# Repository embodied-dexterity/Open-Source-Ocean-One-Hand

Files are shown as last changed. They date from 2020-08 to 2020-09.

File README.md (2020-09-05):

# Open-Source-Ocean-One-Hand
Welcome to the Open Source Ocean One Hand Project. Here are the files you need to create your own Ocean One hand. Each folder is one subassembly, and it 
contains CAD files for each individul parts and the subassembly which are readable by SolidWorks. The folders also contain files for parts that are 
for prototyping, such as 3D printing, laser cutting and rubber casting. \
The instruction manual attached provides not only the assembly instruction, but also the off-the-shelf parts shopping list and some other key protytping notes. \
Please do not hesistate to give us feedbacks or questions regarding this project as we need your help to make this project more accessible to people who would like to learn more about robotics. 
We look forward to all your comments!! \
Thank you for your interest in the Open Source Ocean One Hand Project.

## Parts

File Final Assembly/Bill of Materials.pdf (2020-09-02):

ITEM NO. | PART NUMBER | DESCRIPTION | QTY.
1 | 92290A182 | Shoulder Bolt | 4
2 | Finger Mounting Plate Assembly | | 1
3 | eyehook plate with side slots | | 1
4 | 94150A335 | Hex Nut | 4
5 | Rubber Palm Plate | | 1
6 | 90116A153 | Pan Head Phillips Machine Screw | 7
7 | shaft support | | 1

SOLIDWORKS Educational Product. For Instructional Use Only.

This is a Top Level only part list. To see part lists of sub-assembly, please refer to the Bill of Materials in the folder of each sub-assembly

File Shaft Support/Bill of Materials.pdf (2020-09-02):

ITEM NO. | PART NUMBER | DESCRIPTION | QTY.
1 | Shaft Suppot | | 1
2 | Torsional Spring Hub | | 3
3 | 7532K11 | Thrust Washer | 4
4 | Custom D-Shaft | | 1
5 | 7763K1 | Bushing | 2
6 | 30425T23 | Eye Hook for Wood | 3

SOLIDWORKS Educational Product. For Instructional Use Only.

This is a Top Level only part list. To see part lists of sub-assembly, please refer to the Bill of Materials in the folder of each sub-assembly

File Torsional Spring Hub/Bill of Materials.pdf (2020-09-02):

ITEM NO. | PART NUMBER | DESCRIPTION | QTY.
1 | Torsional Spring Coupler | | 1
2 | SpringInsideSpacer | | 1
3 | 7532K11 | Thrust Washer | 1
4 | Torsional Spring Hub Pulley | | 1
5 | 9287K143 | Torsional Spring | 1
6 | 6679K11 | Bushing | 1
7 | 93935A310 | Thin Hex Nut | 1
8 | 92029A097 | Cup Point Set Screw | 1
9 | 93600A200 | Dowel Pin | 1

SOLIDWORKS Educational Product. For Instructional Use Only.

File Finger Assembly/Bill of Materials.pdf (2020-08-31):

ITEM NO. | PART NUMBER | DESCRIPTION | QTY.
1 | distal finger | | 1
2 | mid finger | | 1
3 | 93600A195 | Dowel Pin | 1
4 | 93600A376 | Dowel Pin | 1
5 | 93600A246 | Dowel Pin | 1
6 | 93600A163 | Dowel Pin | 2
7 | 93600A249 | Dowel Pin | 2
8 | 93600A233 | Dowel Pin | 2
9 | 93600A238 | Dowel Pin | 2
10 | 93600A223 | Dowel Pin | 1
11 | Distal Flexure | | 2
12 | Middle Flexure | | 2
13 | 92398A121 | Hex Shaped Insert | 4
14 | 90116A153 | Pan Head Philips Machine Screw | 4
15 | Proximal Joint | | 1
16 | Base Joint | | 1
17 | 6362K1 | Dry Running Sleeve Bearing | 2
18 | 90101A009 | Nylon Inser locknut | 1
19 | 94035A172 | Shoulder Screw | 1
20 | 9287K208 | Torsion Spring | 1

SOLIDWORKS Educational Product. For Instructional Use Only.

There are extra parts not listed here as they are not in the SolidWorks Assembly but they are listed in the instruction.

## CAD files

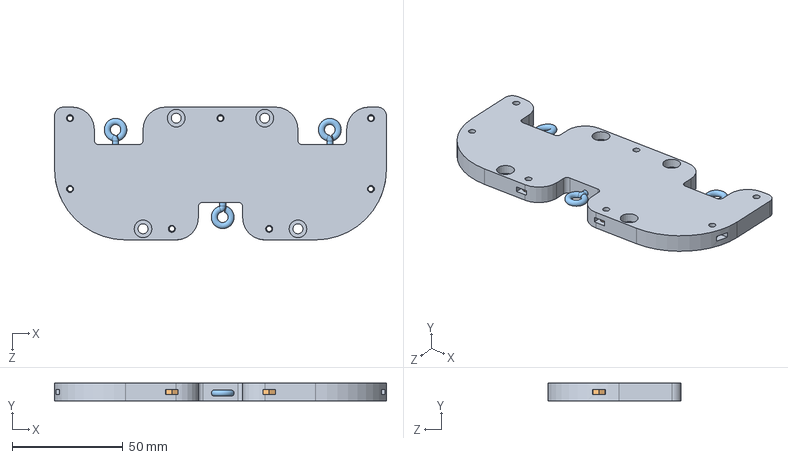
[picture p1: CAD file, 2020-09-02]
Eyehook Plate/eyehook plate with side slots.SLDASM
150.0 x 8.00 x 60.0 mm
eyeHookMountingPlate
94150A325_TYPE 316 STAINLESS STEEL HEX NUT x 7
eyeHook_forWood_30425T230 x 3

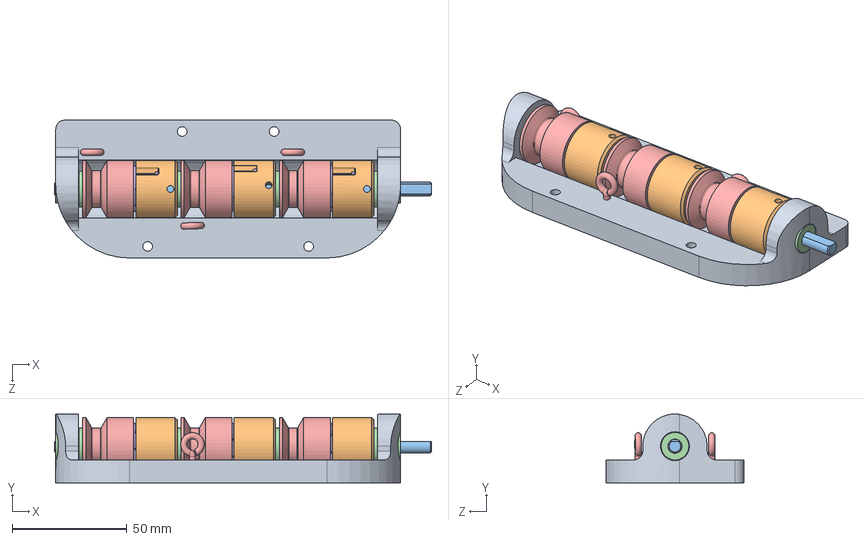
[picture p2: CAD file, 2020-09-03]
Final Assembly/shaft support.SLDASM
164.0 x 30.0 x 60.0 mm
Shaft Suppot
Torsional Spring Coupler x 3
SpringInsideSpacer x 3
6mmThrustWasher_7532K110 x 7
Torsional Spring Hub Pulley x 3
torsionalSpring_9287K143 x 3
m6Bushing_6679K110 x 3
93935A310_TYPE 316 SS THIN HEX NUT - DIN 439B x 3
92029A097_TYPE 316 STAINLESS STEEL CUP POINT SET SCREW x 3
93600A200_METRIC TYPE 316 STAINLESS STEEL DOWEL PIN x 3
Custom D-Shaft
m6Bushing_7763K100 x 2
eyeHook_forWood_30425T230 x 3

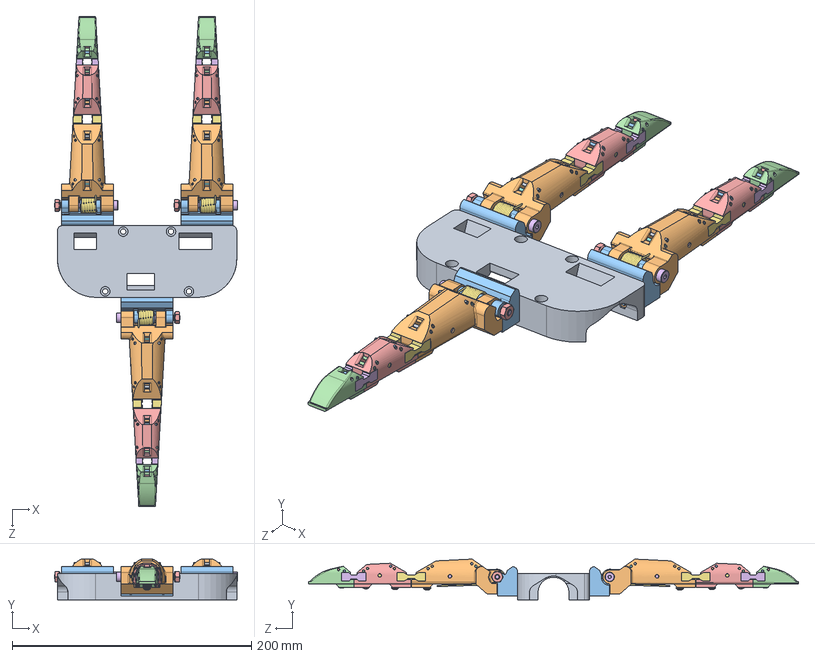
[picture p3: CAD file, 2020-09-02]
Final Assembly/Finger Mounting Plate Assembly.SLDASM
153.2 x 34.2 x 409.8 mm
Finger Mounting plate
94150A325_TYPE 316 STAINLESS STEEL HEX NUT x 6
M3x25_flathead_92010A130 x 6
distal finger x 3
mid finger x 3
93600A195_316 STAINLESS STEEL DOWEL PIN x 3
93600A376_METRIC TYPE 316 STAINLESS STEEL DOWEL PIN (1) x 3
93600A246_316 STAINLESS STEEL DOWEL PIN x 3
93600A163_316 STAINLESS STEEL DOWEL PIN x 6
93600A249_METRIC TYPE 316 STAINLESS STEEL DOWEL PIN x 6
93600A233_METRIC TYPE 316 STAINLESS STEEL DOWEL PIN x 6
93600A238_METRIC TYPE 316 STAINLESS STEEL DOWEL PIN x 6
93600A223_METRIC TYPE 316 STAINLESS STEEL DOWEL PIN x 3
Distal Flexure x 6
Middle Flexure x 6
92398A121_18-8 SS TWIST-RESISTANT HEX-SHAPED INSERTS (1) x 12
90116A153_METRIC 316 SS PAN HEAD PHILLIPS MACHINE SCREW x 12
Proximal Joint x 3
Base Joint x 3
6362K100_WATER-RESISTANT DRY-RUNNING SLEEVE BEARING (1) x 6
90101A009_TYPE 18-8 SS THIN NYLON-INSERT LOCKNUT x 3
94035A172_18-8 STAINLESS STEEL PRECISION SHOULDER SCREW (1) x 3
9287K208_302 STAINLESS STEEL TORSION SPRING x 3

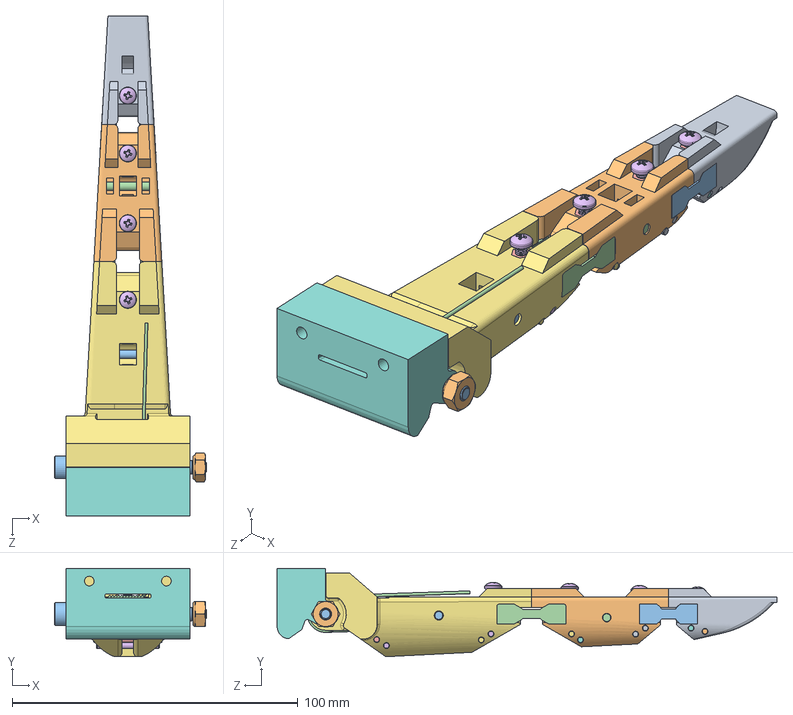
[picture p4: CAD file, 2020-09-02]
Finger Mounting Plate/Finger Assembly.SLDASM
53.2 x 30.9 x 174.9 mm
distal finger
mid finger
93600A195_316 STAINLESS STEEL DOWEL PIN
93600A376_METRIC TYPE 316 STAINLESS STEEL DOWEL PIN (1)
93600A246_316 STAINLESS STEEL DOWEL PIN
93600A163_316 STAINLESS STEEL DOWEL PIN x 2
93600A249_METRIC TYPE 316 STAINLESS STEEL DOWEL PIN x 2
93600A233_METRIC TYPE 316 STAINLESS STEEL DOWEL PIN x 2
93600A238_METRIC TYPE 316 STAINLESS STEEL DOWEL PIN x 2
93600A223_METRIC TYPE 316 STAINLESS STEEL DOWEL PIN
Distal Flexure x 2
Middle Flexure x 2
92398A121_18-8 SS TWIST-RESISTANT HEX-SHAPED INSERTS (1) x 4
90116A153_METRIC 316 SS PAN HEAD PHILLIPS MACHINE SCREW x 4
Proximal Joint
Base Joint
6362K100_WATER-RESISTANT DRY-RUNNING SLEEVE BEARING (1) x 2
90101A009_TYPE 18-8 SS THIN NYLON-INSERT LOCKNUT
94035A172_18-8 STAINLESS STEEL PRECISION SHOULDER SCREW (1)
9287K208_302 STAINLESS STEEL TORSION SPRING

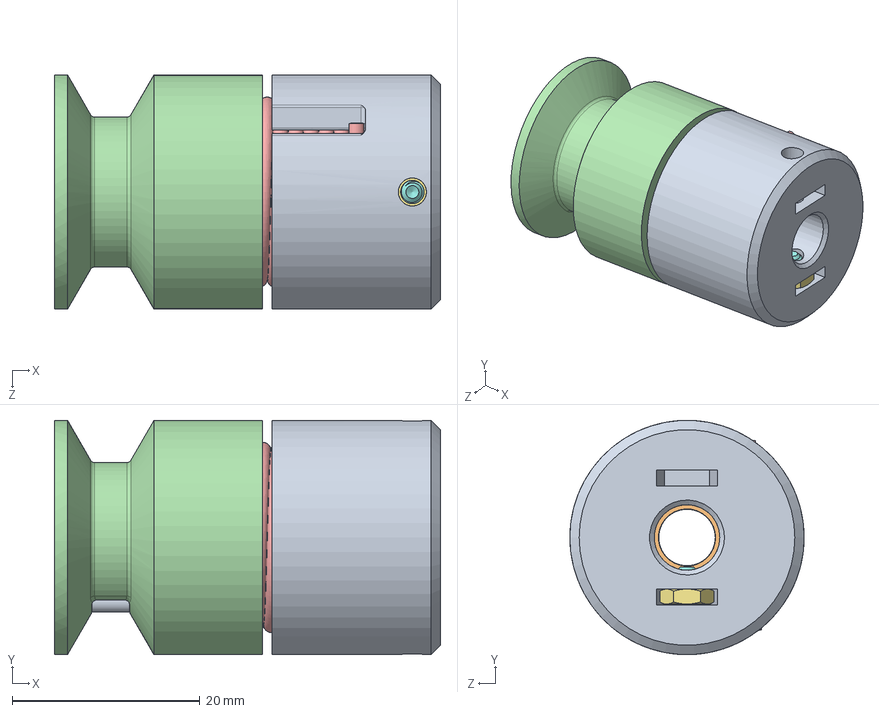
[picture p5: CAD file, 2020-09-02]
Shaft Support/Torsional Spring Hub.SLDASM
41.2 x 25.0 x 25.0 mm
Torsional Spring Coupler
SpringInsideSpacer
6mmThrustWasher_7532K110
Torsional Spring Hub Pulley
torsionalSpring_9287K143
m6Bushing_6679K110
93935A310_TYPE 316 SS THIN HEX NUT - DIN 439B
92029A097_TYPE 316 STAINLESS STEEL CUP POINT SET SCREW
93600A200_METRIC TYPE 316 STAINLESS STEEL DOWEL PIN

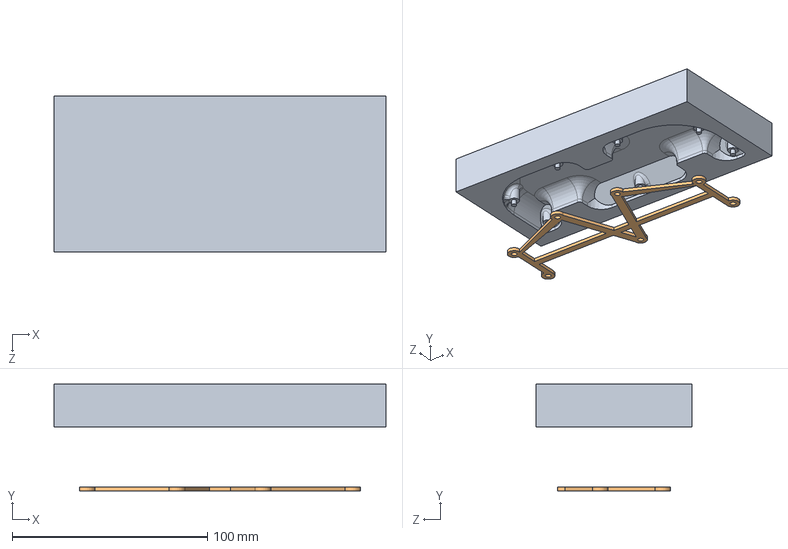
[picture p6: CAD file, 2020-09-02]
Final Assembly/Embedded plate for palm plate.SLDASM
170.0 x 54.6 x 80.0 mm
Rubber Palm Plate 3d print negative mold
palm plate holder

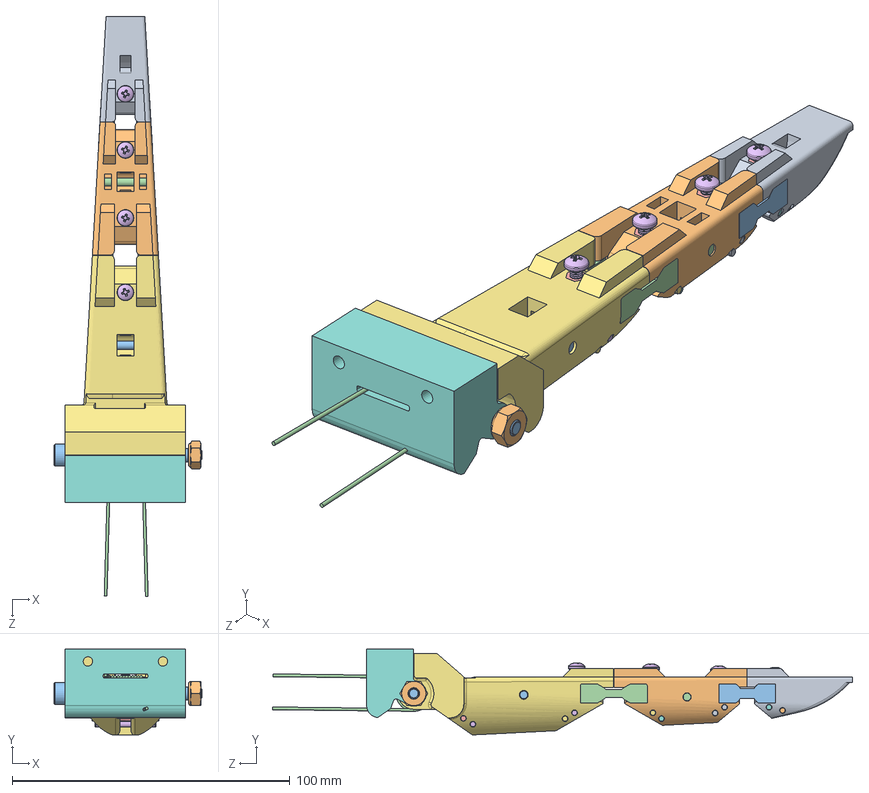
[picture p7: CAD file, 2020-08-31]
Finger Assembly/Finger Assembly.SLDASM
53.2 x 30.9 x 208.8 mm
distal finger
mid finger
93600A195_316 STAINLESS STEEL DOWEL PIN
93600A376_METRIC TYPE 316 STAINLESS STEEL DOWEL PIN (1)
93600A246_316 STAINLESS STEEL DOWEL PIN
93600A163_316 STAINLESS STEEL DOWEL PIN x 2
93600A249_METRIC TYPE 316 STAINLESS STEEL DOWEL PIN x 2
93600A233_METRIC TYPE 316 STAINLESS STEEL DOWEL PIN x 2
93600A238_METRIC TYPE 316 STAINLESS STEEL DOWEL PIN x 2
93600A223_METRIC TYPE 316 STAINLESS STEEL DOWEL PIN
Distal Flexure x 2
Middle Flexure x 2
92398A121_18-8 SS TWIST-RESISTANT HEX-SHAPED INSERTS (1) x 4
90116A153_METRIC 316 SS PAN HEAD PHILLIPS MACHINE SCREW x 4
Proximal Joint
Base Joint
6362K100_WATER-RESISTANT DRY-RUNNING SLEEVE BEARING (1) x 2
90101A009_TYPE 18-8 SS THIN NYLON-INSERT LOCKNUT
94035A172_18-8 STAINLESS STEEL PRECISION SHOULDER SCREW (1)

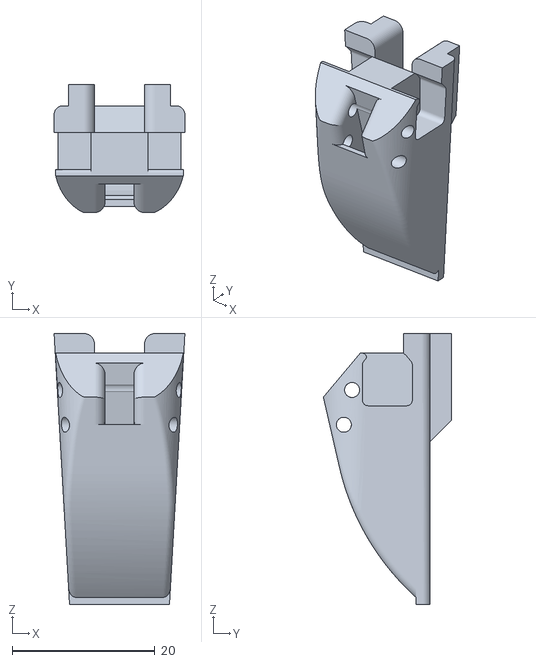
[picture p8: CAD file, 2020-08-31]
Finger Assembly/3D Print STL files and Laser Cut DWG files/distal finger.STL
18.3 x 18.0 x 38.0

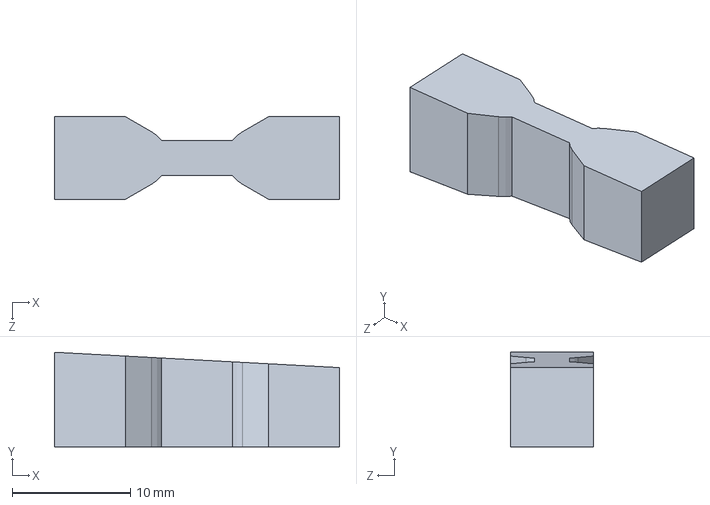
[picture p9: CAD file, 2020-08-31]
Finger Assembly/Middle Flexure.SLDPRT
24.1 x 8.00 x 7.00 mm

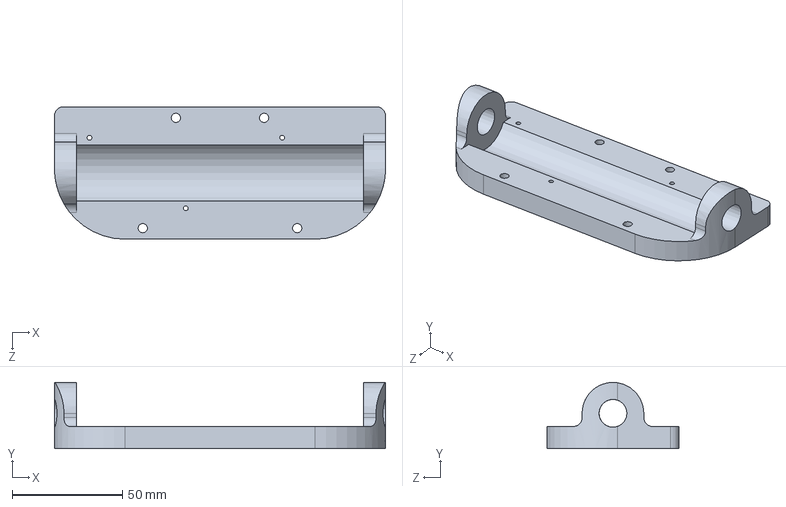
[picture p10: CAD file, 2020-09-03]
Shaft Support/Shaft Suppot.SLDPRT
150.0 x 30.0 x 60.0 mm

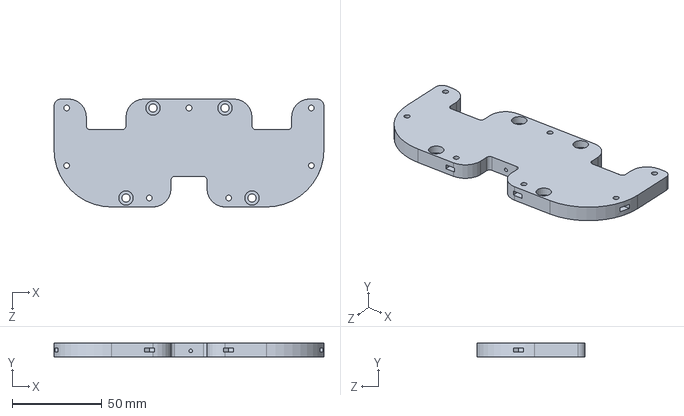
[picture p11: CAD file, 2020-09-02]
Eyehook Plate/eyeHookMountingPlate.SLDPRT
150.0 x 8.00 x 60.0 mm

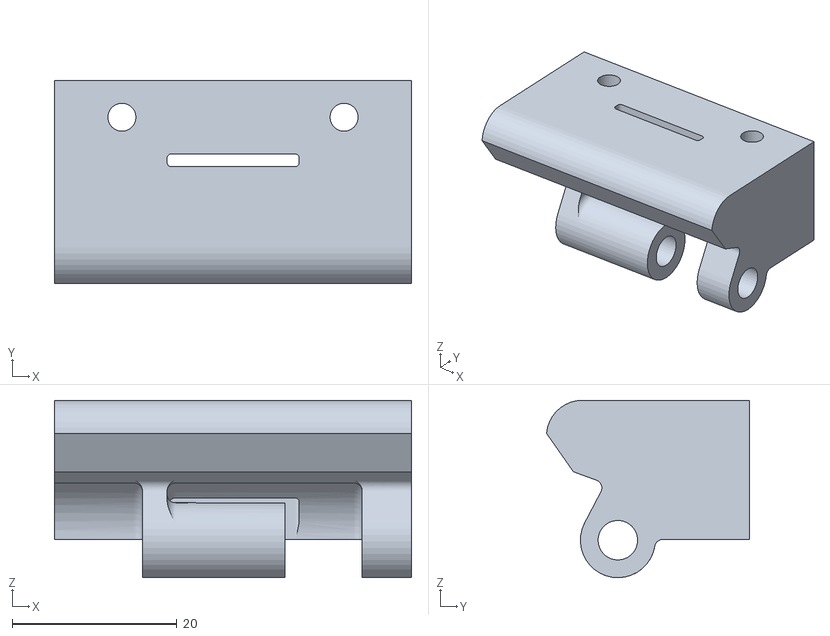
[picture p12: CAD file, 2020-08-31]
Finger Assembly/3D Print STL files and Laser Cut DWG files/Base Joint.STL
43.4 x 24.7 x 21.6

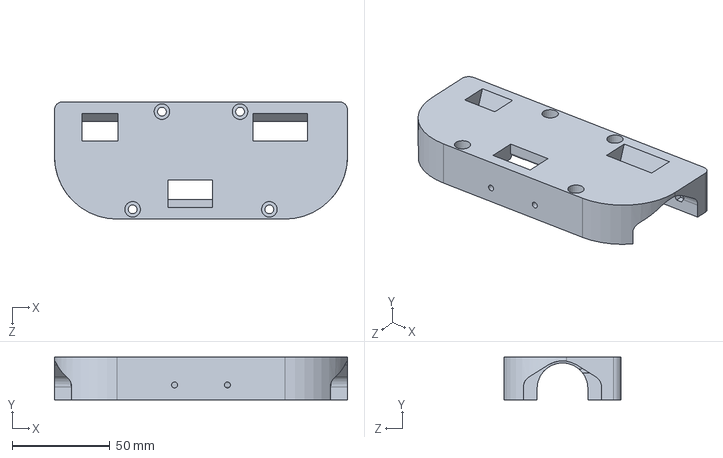
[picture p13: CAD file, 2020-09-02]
Finger Mounting Plate/Finger Mounting Top Plate.SLDPRT
150.0 x 22.0 x 60.0 mm

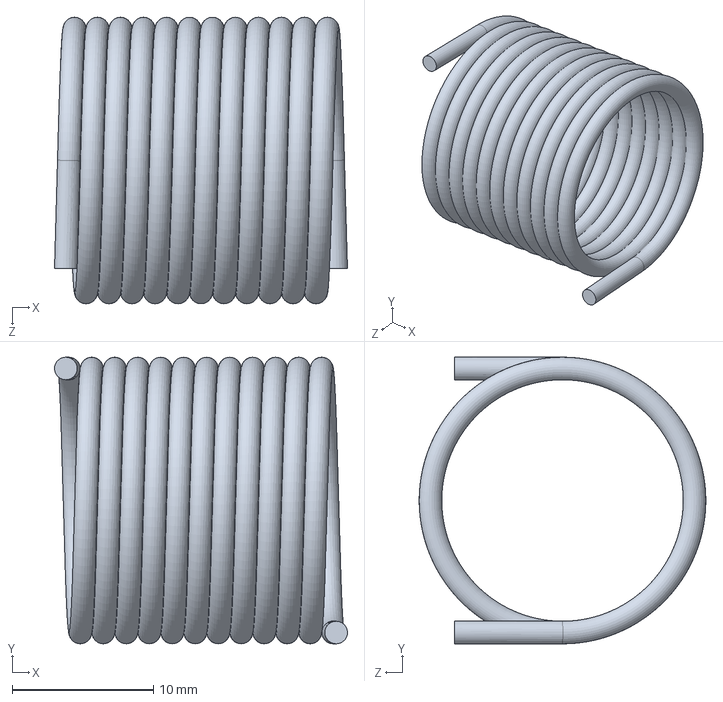
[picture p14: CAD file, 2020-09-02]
Torsional Spring Hub/torsionalSpring_9287K143.SLDPRT
20.7 x 20.3 x 20.3 mm

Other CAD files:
Finger Mounting Plate/Finger Mounting Plate Assembly.SLDASM
Torsional Spring Hub/Torsional Spring Hub.SLDASM
Eyehook Plate/94150A325_TYPE 316 STAINLESS STEEL HEX NUT.SLDPRT
Eyehook Plate/eyeHookMountingPlate.STL
Eyehook Plate/eyeHook_forWood_30425T230.SLDPRT
Final Assembly/90116A153_METRIC 316 SS PAN HEAD PHILLIPS MACHINE SCREW.SLDPRT
Final Assembly/94150A335_TYPE 316 STAINLESS STEEL HEX NUT.SLDPRT
Final Assembly/M4x35_92290A182.SLDPRT
Final Assembly/Rubber Palm Plate 3d print negative mold.SLDPRT
Final Assembly/Rubber Palm Plate.SLDPRT
Final Assembly/palm plate holder.SLDPRT
Finger Assembly/3D Print STL files and Laser Cut DWG files/Flexure Laser Cut Mold.dwg
Finger Assembly/3D Print STL files and Laser Cut DWG files/Proximal Joint.STL
Finger Assembly/3D Print STL files and Laser Cut DWG files/mid finger.STL
Finger Assembly/6362K100_WATER-RESISTANT DRY-RUNNING SLEEVE BEARING (1).SLDPRT
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

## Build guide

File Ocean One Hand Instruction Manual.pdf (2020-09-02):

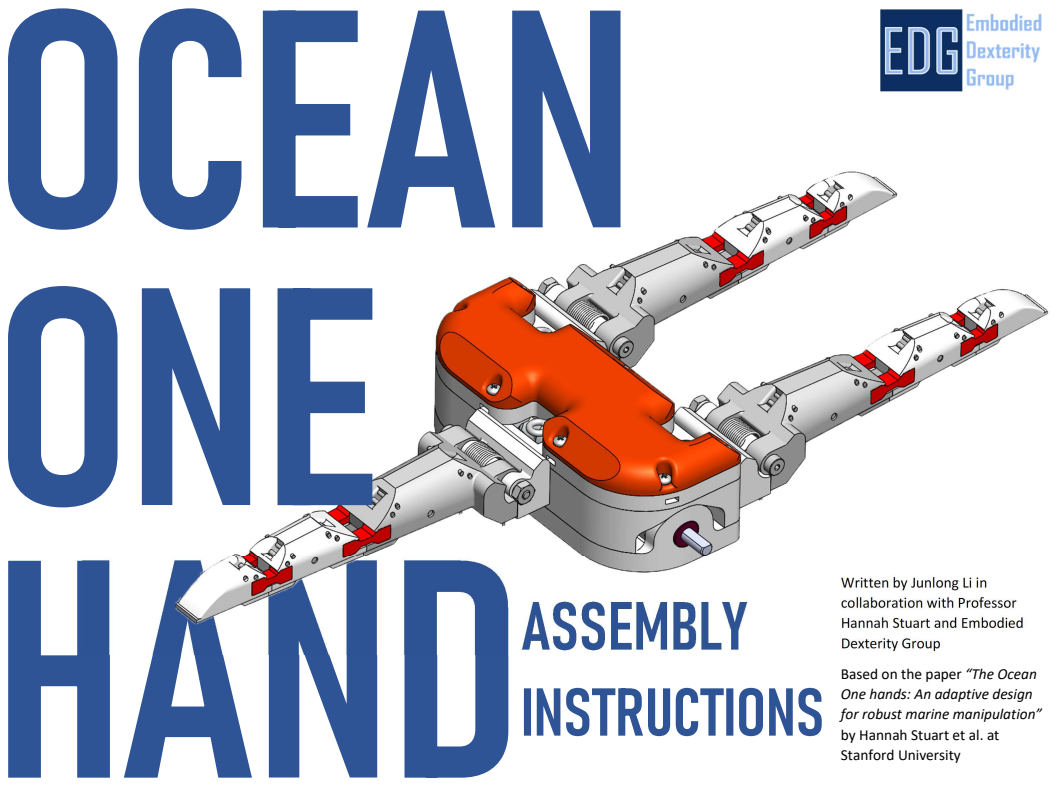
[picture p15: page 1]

Written by Junlong Li in
collaboration with Professor
Hannah Stuart and Embodied
Dexterity Group
Based on the paper “The Ocean
One hands: An adaptive design
for robust marine manipulation”
by Hannah Stuart et al. at
Stanford University

The Ocean One Hand was developed by UC Berkeley Professor Hannah Stuart during her time studying at Stanford University. The Hand was designed for deep-sea exploration with its elastic finger joints and spring transmission which can achieve variety of grasp. With this open source project, Professor Stuart and EDG wish to “empower the general marine science and technology community to start exploring the potential benefits and uses” of this type of compliant grippers.
The first iteration of the Open Source Ocean One Hand Project requires elaborate tools and lab space. It might only be suitable to those with access to a full maker space. A laser cuter, a 3D printer, a power drill and proper chemical disposal are required for this project. The time required to complete this project will depend on the access to tools and off the shelf parts. The estimate cost for raw material of the project, assuming that the main prototyping tools and equipment are $ 350.
Please consider all the above and be prepared before starting the project.
Please submit any questions or feedback to junlong21li@berkeley.edu
Thank you for your interest in testing the first iteration of the Open Source Ocean One Hand.

## MIDDLE JOINT

A2

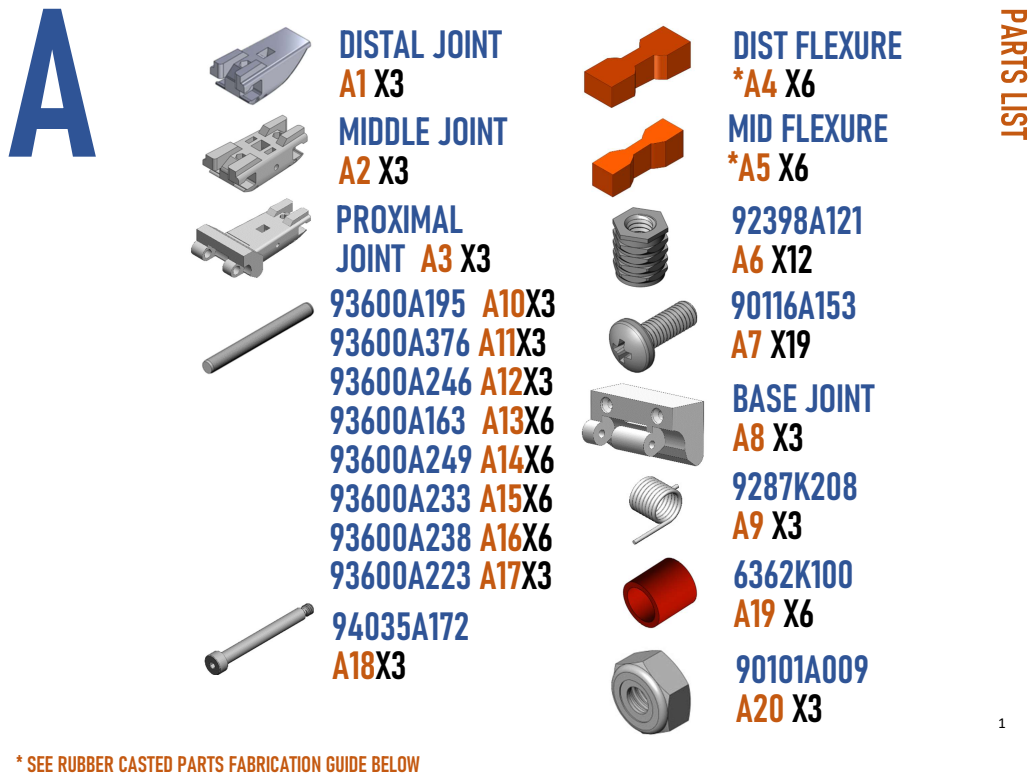
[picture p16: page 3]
3 PROXIMAL JOINT A3; DIST FLEXURE *A4 X6; MID FLEXURE *A5 X6; BASE JOINT A8 X3; DISTAL JOINT A1

* SEE RUBBER CASTED PARTS FABRICATION GUIDE BELOW

## TORSION SPRING HOUSING 1 B1 X3

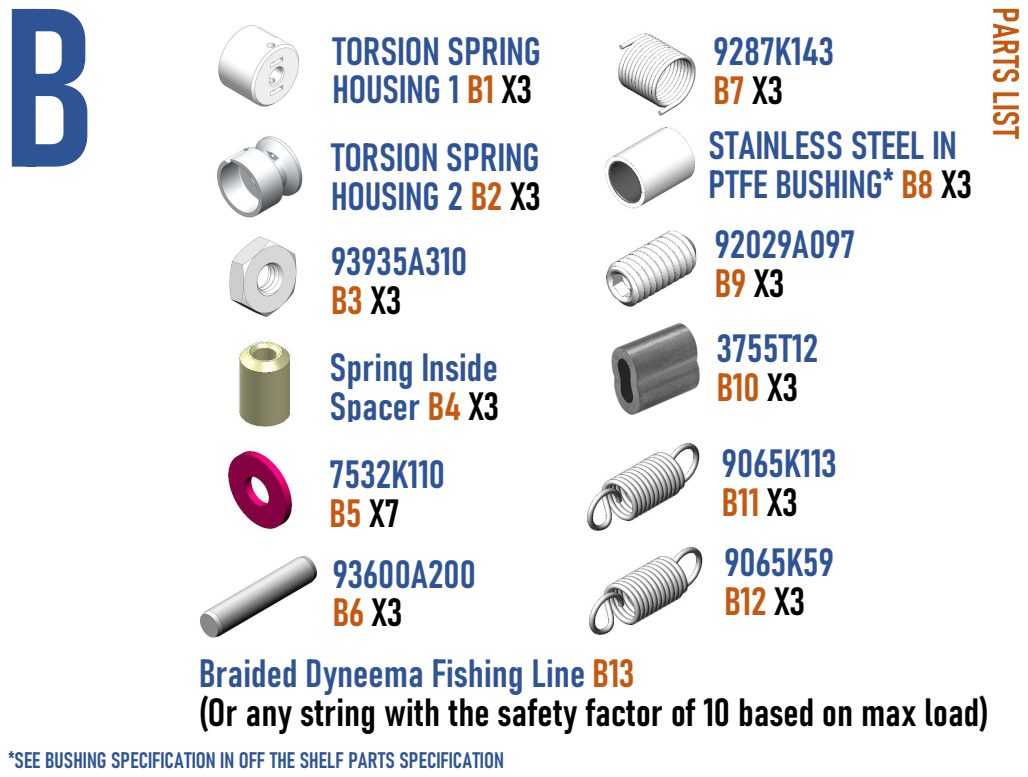
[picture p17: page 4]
TORSION SPRING HOUSING 2 B2 X3; Spring Inside Spacer B4 X3; 9287K143 B7 X3 STAINLESS STEEL IN PTFE BUSHING* B8 X3

Braided Dyneema Fishing Line B13
(Or any string with the safety factor of 10 based on max load)

*SEE BUSHING SPECIFICATION IN OFF THE SHELF PARTS SPECIFICATION

## FINGER MOUNTING PLATE C1 X1

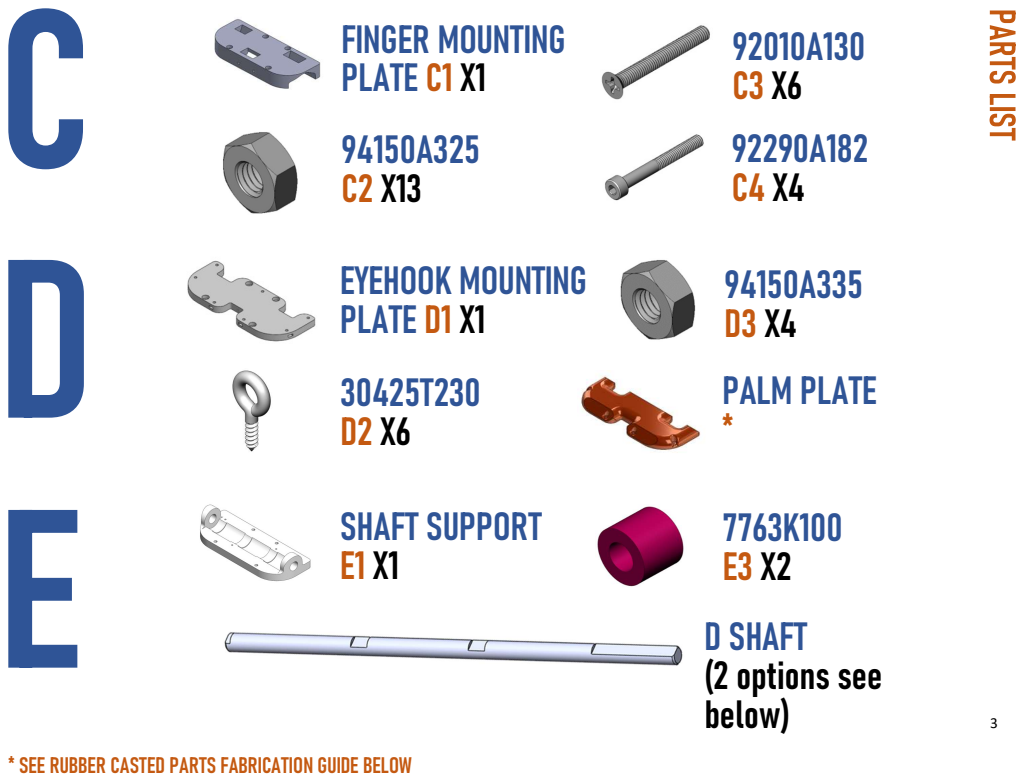
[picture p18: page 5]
EYEHOOK MOUNTING PLATE D1 X1; PALM PLATE *; SHAFT SUPPORT E1 X1; D SHAFT (2 options see below)

* SEE RUBBER CASTED PARTS FABRICATION GUIDE BELOW

## MIDDLE JOINT A2

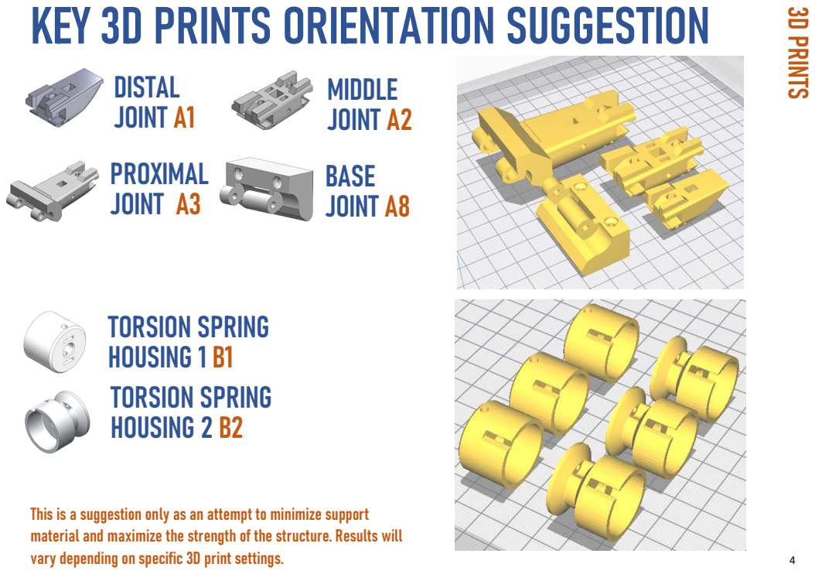
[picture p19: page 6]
DISTAL JOINT A1; PROXIMAL JOINT A3; BASE JOINT A8; TORSION SPRING HOUSING 1 B1 TORSION SPRING HOUSING 2 B2

This is a suggestion only as an attempt to minimize support
material and maximize the strength of the structure. Results will
vary depending on specific 3D print settings.

## 93600A195 A10X3 (3mm DM, 26mm L) @$1.66/PACK OF 1 93600A376 A11X3 (3mm DM, 20mm L) @$4.58/PACK OF 10

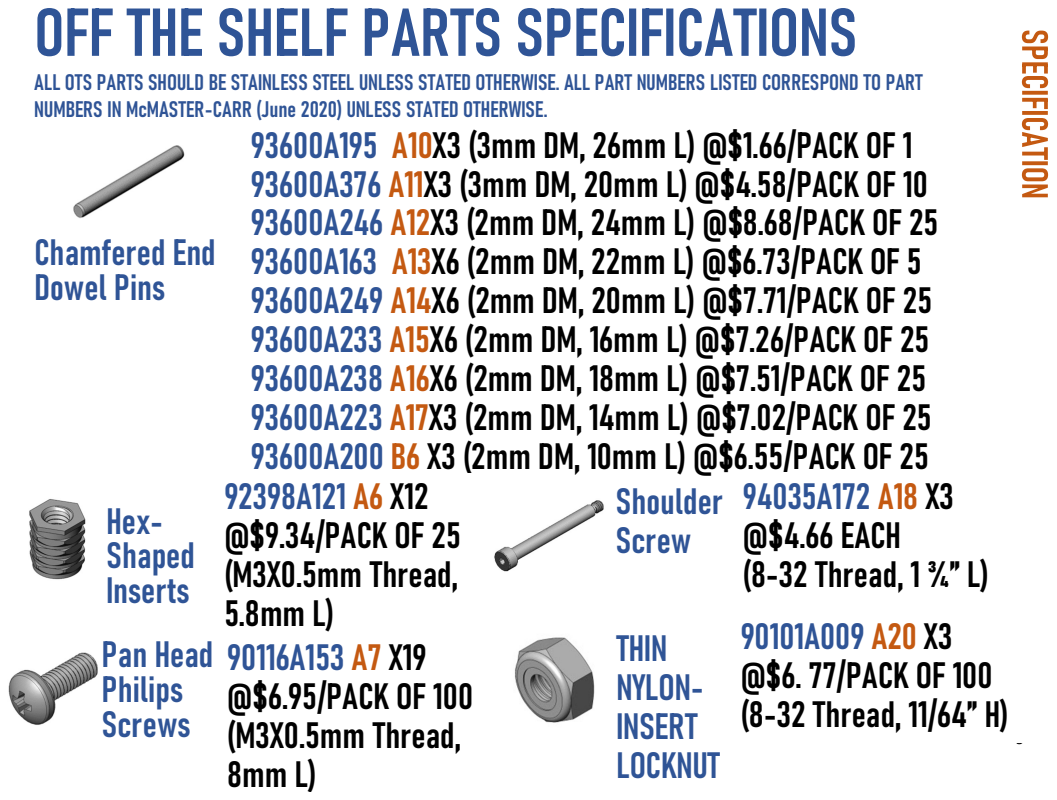
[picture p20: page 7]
THIN NYLON- INSERT; Chamfered End Dowel Pins; Pan Head Philips Screws; Shoulder Screw; 94035A172 A18 X3 @$4.66 EACH (8-32 Thread, 1 ¾” L); 90101A009 A20 X3 @$6. 77/PACK OF 100 (8-32 Thread, 11/64” H)

ALL OTS PARTS SHOULD BE STAINLESS STEEL UNLESS STATED OTHERWISE. ALL PART NUMBERS LISTED CORRESPOND TO PART
NUMBERS IN McMASTER-CARR (June 2020) UNLESS STATED OTHERWISE.

93600A246 A12X3 (2mm DM, 24mm L) @$8.68/PACK OF 25
93600A163 A13X6 (2mm DM, 22mm L) @$6.73/PACK OF 5
93600A249 A14X6 (2mm DM, 20mm L) @$7.71/PACK OF 25
93600A233 A15X6 (2mm DM, 16mm L) @$7.26/PACK OF 25
93600A238 A16X6 (2mm DM, 18mm L) @$7.51/PACK OF 25
93600A223 A17X3 (2mm DM, 14mm L) @$7.02/PACK OF 25
93600A200 B6 X3 (2mm DM, 10mm L) @$6.55/PACK OF 25
@$9.34/PACK OF 25
(M3X0.5mm Thread,
@$6.95/PACK OF 100

Hex-Shaped Inserts

LOCKNUT

## Thin Hex Nuts

## 93935A310 B3 X3 @$5.34/PACK OF 50

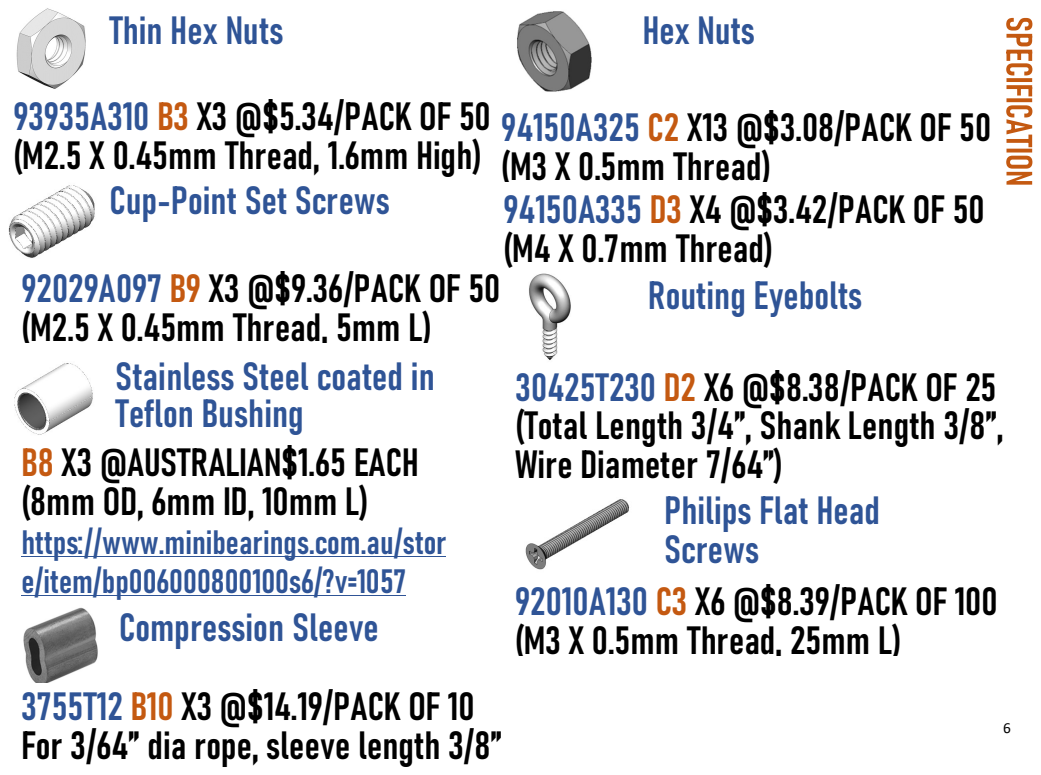
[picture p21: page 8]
(M2.5 X 0.45mm Thread, 1.6mm High); Hex Nuts; Routing Eyebolts; 92010A130 C3 X6 @$8.39/PACK OF 100

94150A325 C2 X13 @$3.08/PACK OF 50 (M3 X 0.5mm Thread)

Cup-Point Set Screws | 94150A335 D3 X4 @$3.42/PACK OF 50 (M4 X 0.7mm Thread)

92029A097 B9 X3 @$9.36/PACK OF 50
(M2.5 X 0.45mm Thread, 5mm L)
Stainless Steel coated in
Teflon Bushing
B8 X3 @AUSTRALIAN$1.65 EACH
https://www.minibearings.com.au/stor
e/item/bp006000800100s6/?v=1057
(M3 X 0.5mm Thread, 25mm L) Compression Sleeve

30425T230 D2 X6 @$8.38/PACK OF 25
(Total Length 3/4”, Shank Length 3/8”,
Wire Diameter 7/64”)

Philips Flat Head
Screws

3755T12 B10 X3 @$14.19/PACK OF 10
For 3/64” dia rope, sleeve length 3/8”

## 92290A182 C4 X4 @$9.26/PACK OF 25 (M4 X 0.7mm Thread, 35mm L)

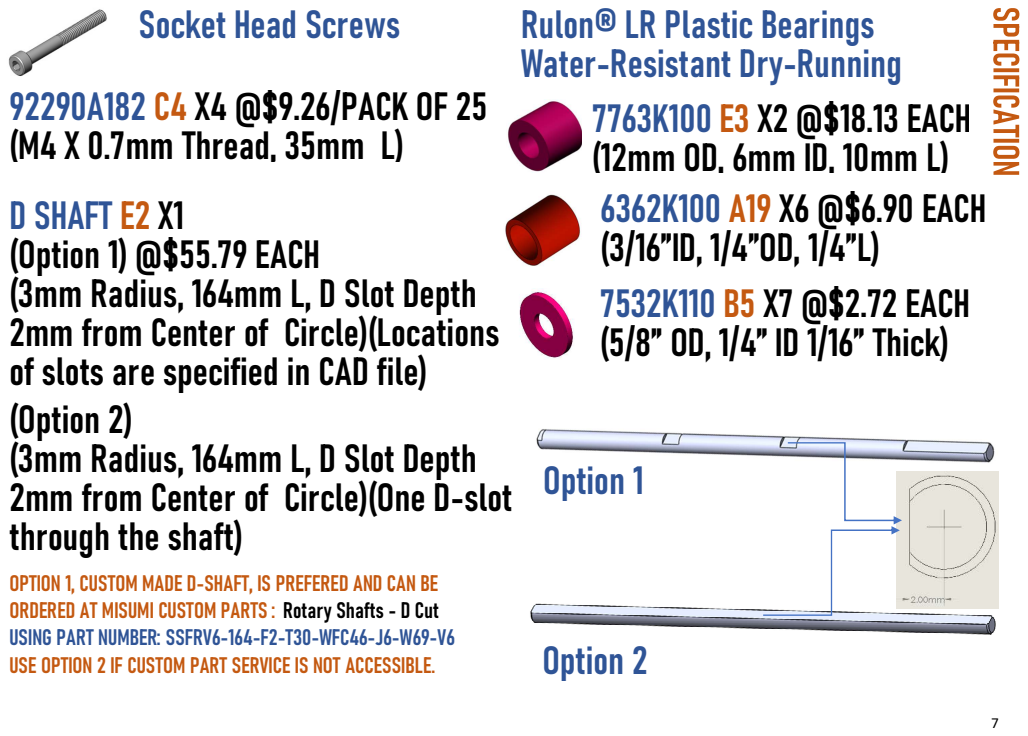
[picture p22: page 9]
Option 1; Option 2

Socket Head Screws

Rulon® LR Plastic Bearings
Water-Resistant Dry-Running
7763K100 E3 X2 @$18.13 EACH
6362K100 A19 X6 @$6.90 EACH
7532K110 B5 X7 @$2.72 EACH
(5/8” OD, 1/4” ID 1/16” Thick)

D SHAFT E2 X1
(Option 1) @$55.79 EACH
(3mm Radius, 164mm L, D Slot Depth
2mm from Center of Circle)(Locations
of slots are specified in CAD file)
(Option 2)
2mm from Center of Circle)(One D-slot
through the shaft)

OPTION 1, CUSTOM MADE D-SHAFT, IS PREFERED AND CAN BE
ORDERED AT MISUMI CUSTOM PARTS : Rotary Shafts - D Cut
USING PART NUMBER: SSFRV6-164-F2-T30-WFC46-J6-W69-V6
USE OPTION 2 IF CUSTOM PART SERVICE IS NOT ACCESSIBLE.

## 360⁰ Deflection Left-Hand Wound Torsion

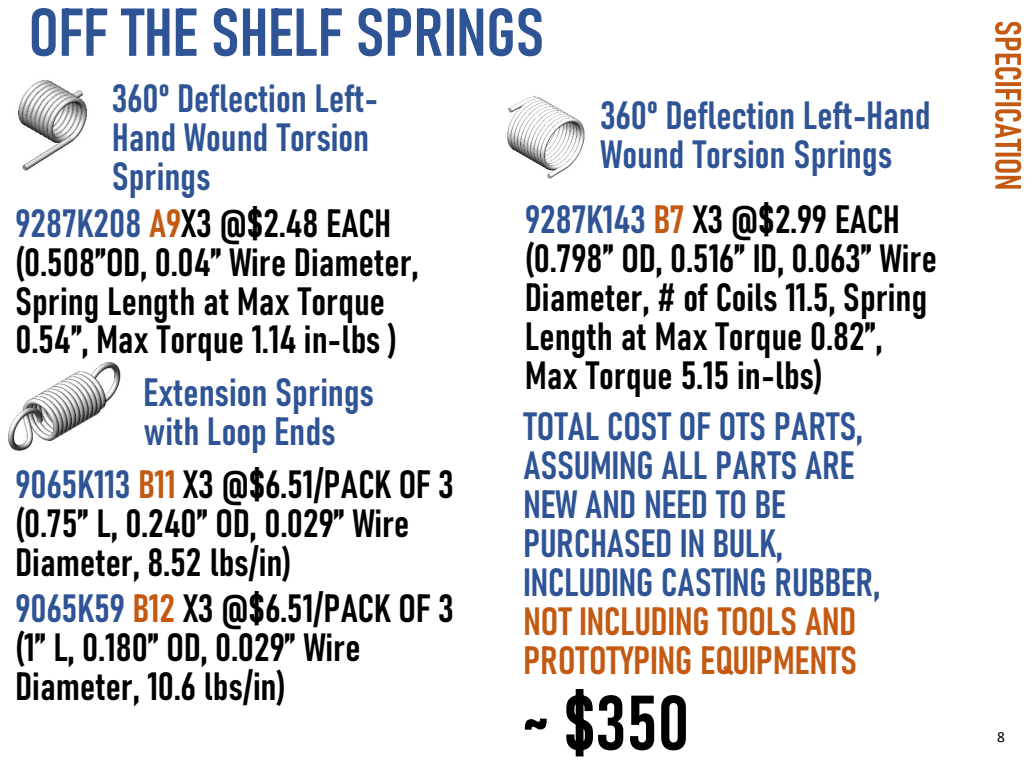
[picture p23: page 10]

360⁰ Deflection Left-Hand
Wound Torsion Springs
9287K143 B7 X3 @$2.99 EACH
(0.798” OD, 0.516” ID, 0.063” Wire
Diameter, # of Coils 11.5, Spring
Length at Max Torque 0.82”,
Max Torque 5.15 in-lbs)
TOTAL COST OF OTS PARTS,
ASSUMING ALL PARTS ARE
NEW AND NEED TO BE
PURCHASED IN BULK,
INCLUDING CASTING RUBBER,
NOT INCLUDING TOOLS AND
PROTOTYPING EQUIPMENTS

Springs
9287K208 A9X3 @$2.48 EACH
(0.508”OD, 0.04” Wire Diameter,
Spring Length at Max Torque
0.54”, Max Torque 1.14 in-lbs )

Extension Springs
with Loop Ends

9065K113 B11 X3 @$6.51/PACK OF 3
(0.75” L, 0.240” OD, 0.029” Wire
Diameter, 8.52 lbs/in)
9065K59 B12 X3 @$6.51/PACK OF 3
(1” L, 0.180” OD, 0.029” Wire
Diameter, 10.6 lbs/in)

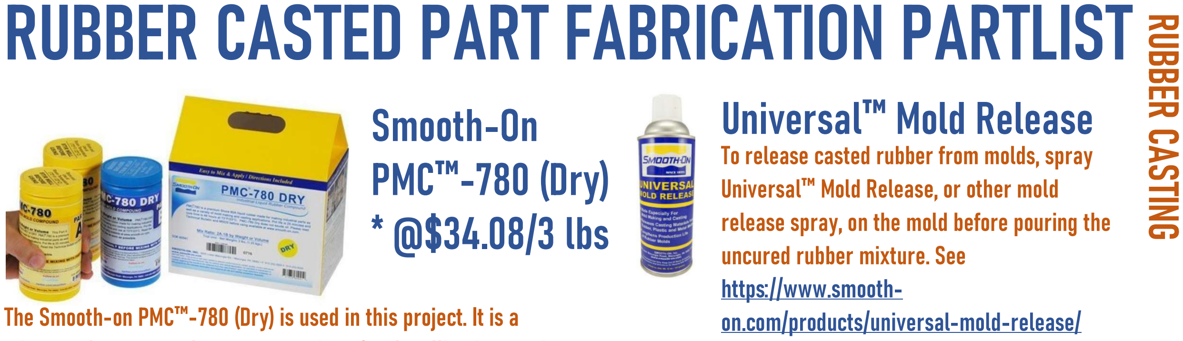
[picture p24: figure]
Smooth-On PMC™-780 (Dry) * @$34.08/3 lbs; Universal™ Mold Release; Universal™ Mold Release, or other mold; uncured rubber mixture. See https://www.smooth- on.com/products/universal-mold-release/

9

The Smooth-on PMC™-780 (Dry) is used in this project. It is a mixture of two parts that cure over time. See handling instruction on https://www.smooth-on.com/products/pmc-780-dry/
* low-cost alternative: Econ™80 from Smooth-On @$27.78/1.9 lbs

To release casted rubber from molds, spray

release spray, on the mold before pouring the

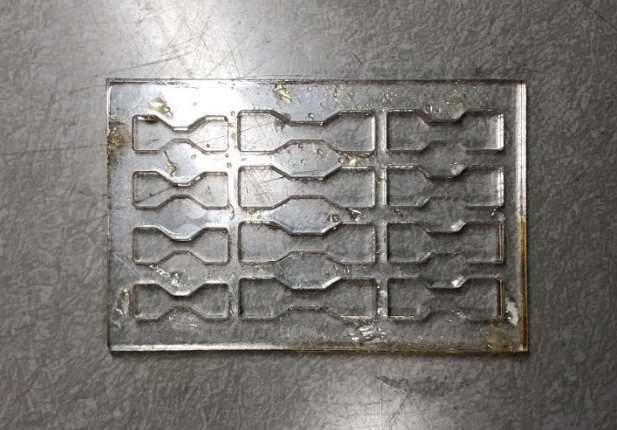
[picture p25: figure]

## Finger Flexure Mold & Palm Mold

Finger flexure mold is laser cut using 5mm acrylic. Palm mold is 3d printed. Both flexures and palm can be directly printed using NinjaFlex or other flexible 3D print material. Flexure mold template is located in the Finger Assembly folder and Palm mold is located in the Full Assembly folder.
For casting, you will also need:
- Disposable Cup for resin mixture
- Popsicles stick for mixing
- Nitrile Gloves
- Digital Scale

*For 3D printed Flexure using FDM 3D printing, it is
recommended that grain
direction is parallel to the length of the flexure as shown.

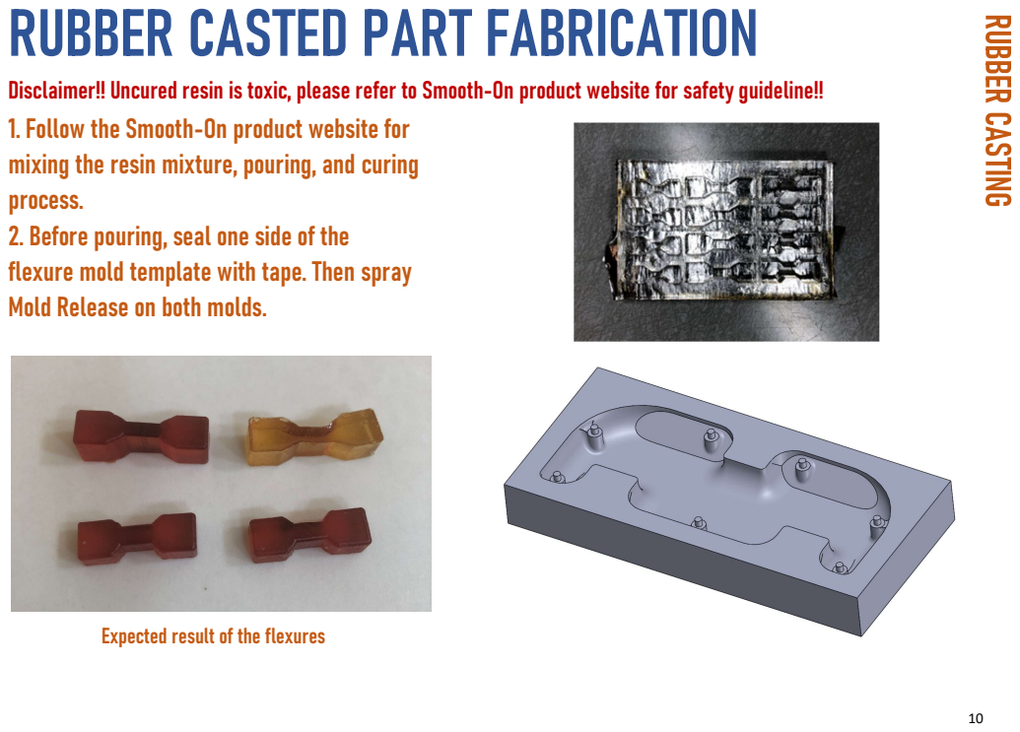
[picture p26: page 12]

Disclaimer!! Uncured resin is toxic, please refer to Smooth-On product website for safety guideline!!
1. Follow the Smooth-On product website for
mixing the resin mixture, pouring, and curing
process.
2. Before pouring, seal one side of the
flexure mold template with tape. Then spray
Mold Release on both molds.

Expected result of the flexures

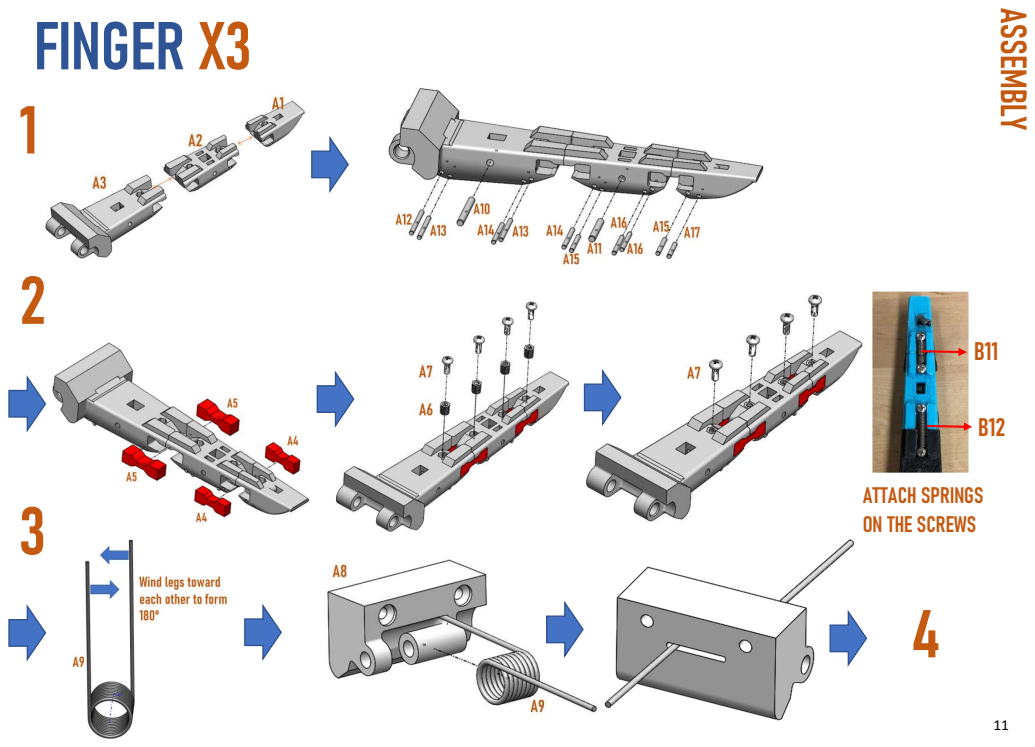
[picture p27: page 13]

ATTACH SPRINGS
ON THE SCREWS

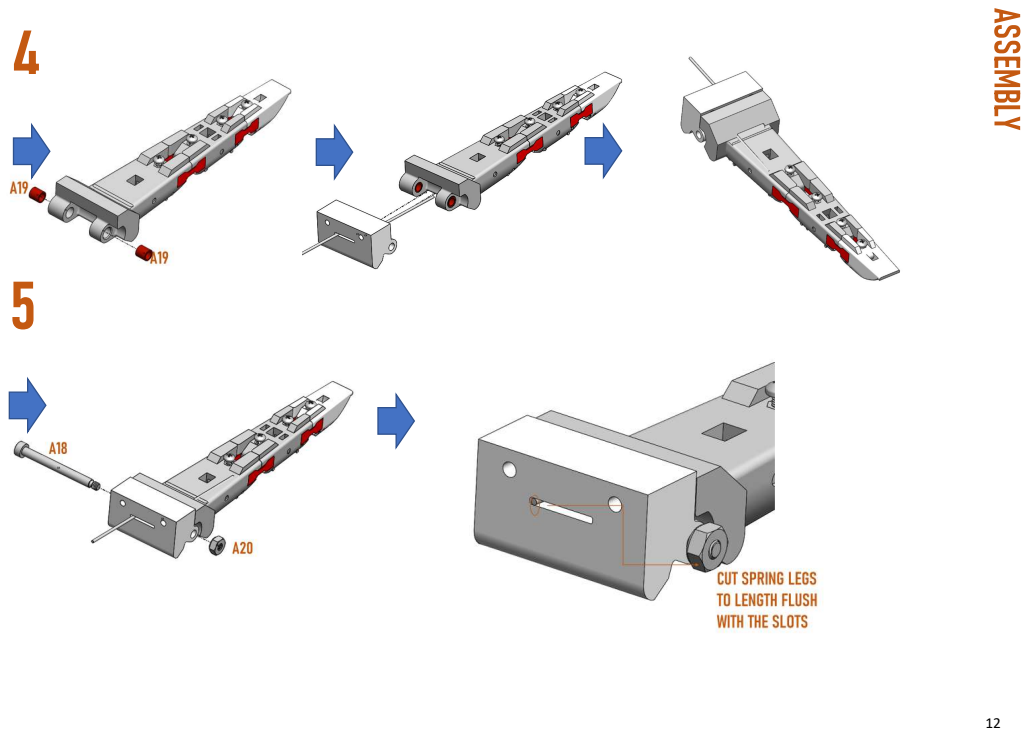
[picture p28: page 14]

13

1. Put dowel pins into the respective holes on the fingers.
2. Insert flexures A5 and A4 into the finger to connect the joints.
3. Insert A6 threaded inserts into the hex slots. (If the slots are undersize, heat up the threaded inserts and push them into the slots as the hot metal melts the plastic)
4. Use A7 screws to fix the two ends of springs. (Between A1 and A2, use B11, between A2 and A3, use B12)

### 5. Wind A9 Torsion Spring inward to create 180⁰ between legs

6. Place A9 torsion springs through the slot of the base joint.

### 7. Fit A19 bushings into the holes of the A3 finger joint

8. Fit the other legs of the torsion springs into the slots of the A3 finger joint.
9. Insert A18 pin into the joint to connect the base joint and A3 finger joint, tighten A20 locknut and cut off the excess length of the legs of the torsion springs.

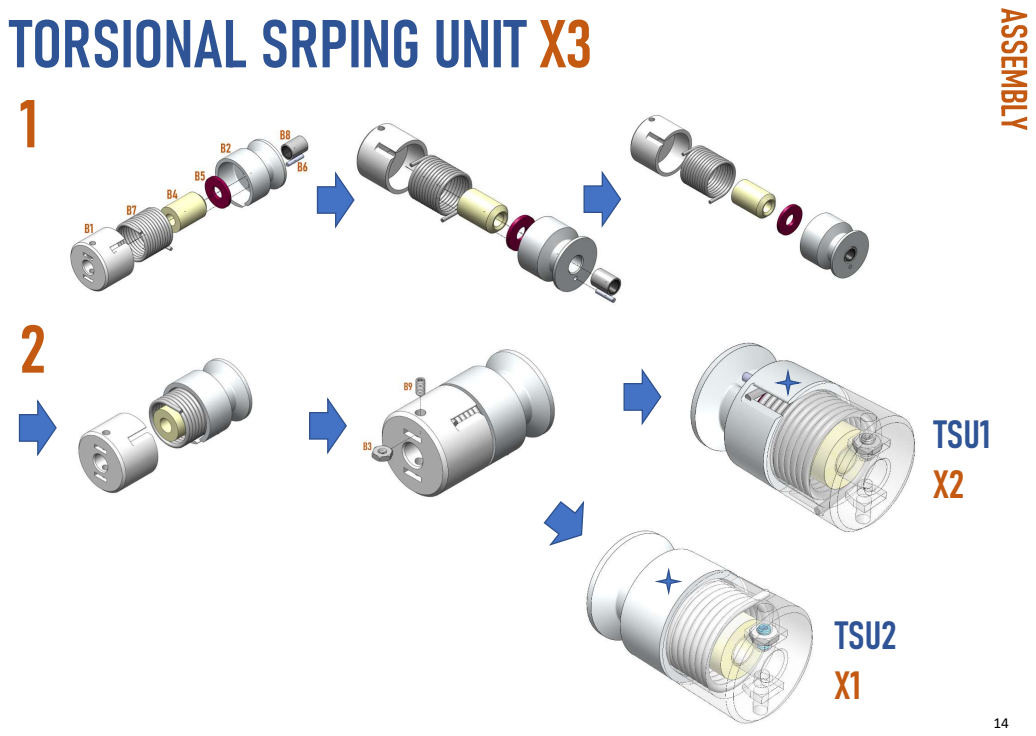
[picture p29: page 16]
TSU1 X2; TSU2 X1

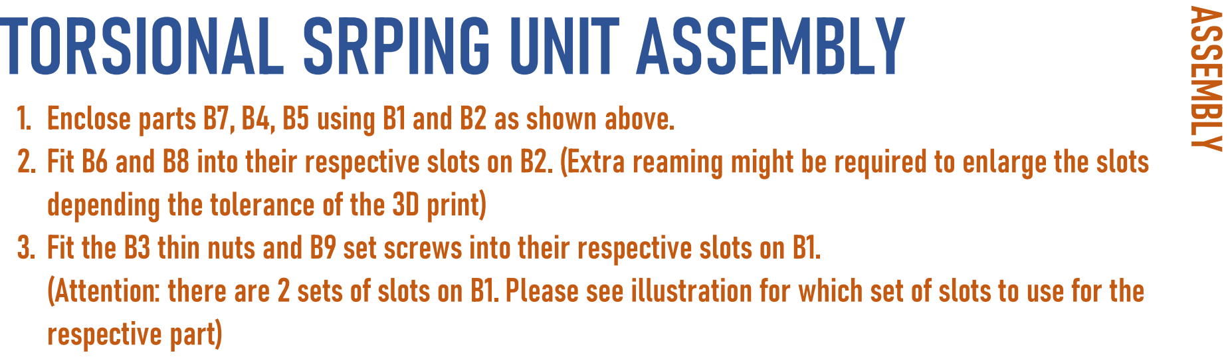
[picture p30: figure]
respective part)

15

1. Enclose parts B7, B4, B5 using B1 and B2 as shown above.
2. Fit B6 and B8 into their respective slots on B2. (Extra reaming might be required to enlarge the slots depending the tolerance of the 3D print)
3. Fit the B3 thin nuts and B9 set screws into their respective slots on B1.
(Attention: there are 2 sets of slots on B1. Please see illustration for which set of slots to use for the

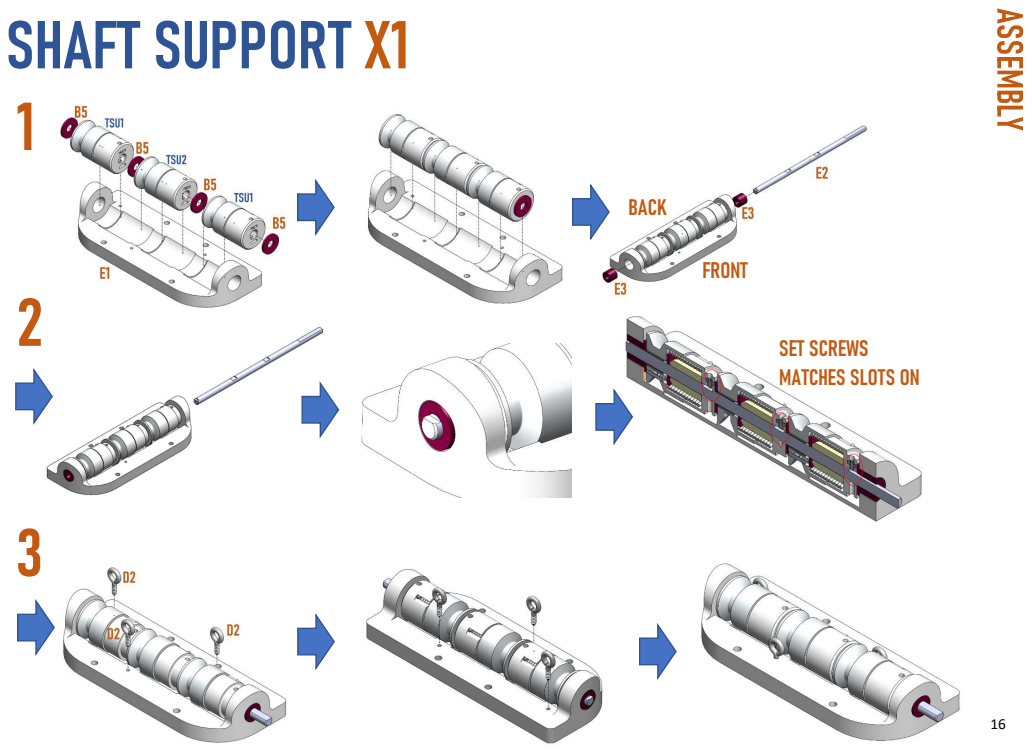
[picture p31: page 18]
FRONT; BACK

SET SCREWS
MATCHES SLOTS ON

17

1. Align parts in the order shown above and leave the parts in E1 the shaft support, and all set screws facing up.
2. Fit E3 bushing into the slots on the two ends of the shaft support.
3. Facing the front of the shaft support, fit E2 D-shaft through the bushing on the right end of the shaft support with the shorter end of the D-shaft.
4. Continue threading the D shaft through the parts until the short end of the D-shaft is flushed with the end of the bushing.
5. Turn all three torsion spring units so that the they are aligned with the flat surface of the D-shaft.
6. Slowly screw in the set screws and wiggle the D-shaft to make sure the set screws are in the D-shaft slots. (As illustrated above)
7. Screw on D2 eyehooks on the shaft support.

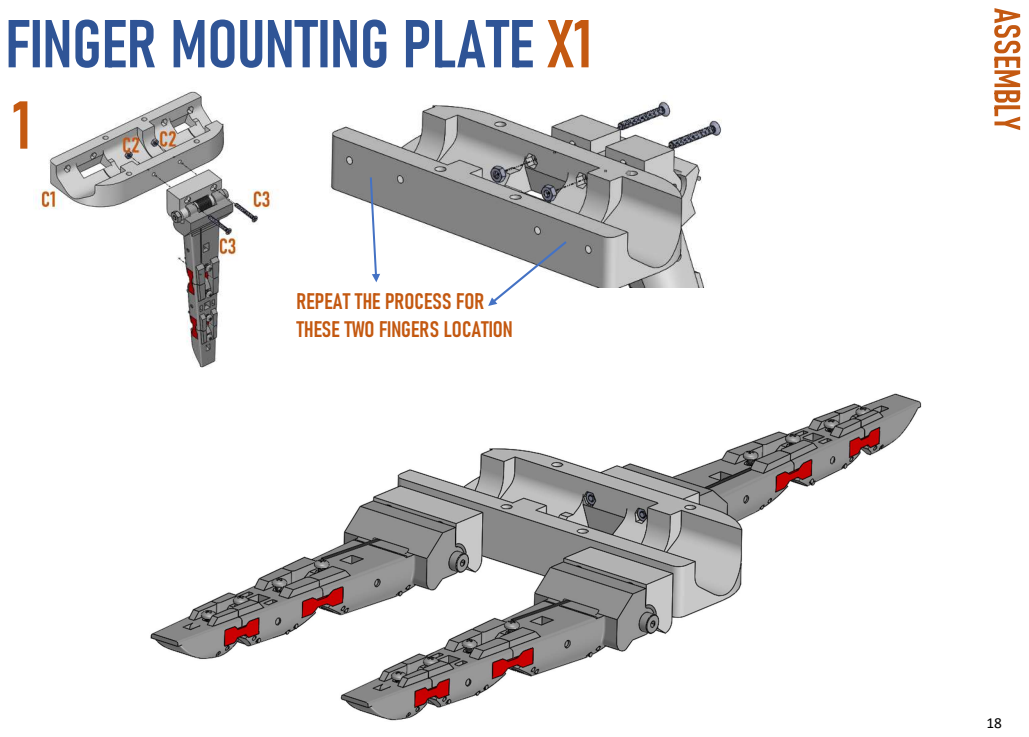
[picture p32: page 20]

REPEAT THE PROCESS FOR
THESE TWO FINGERS LOCATION

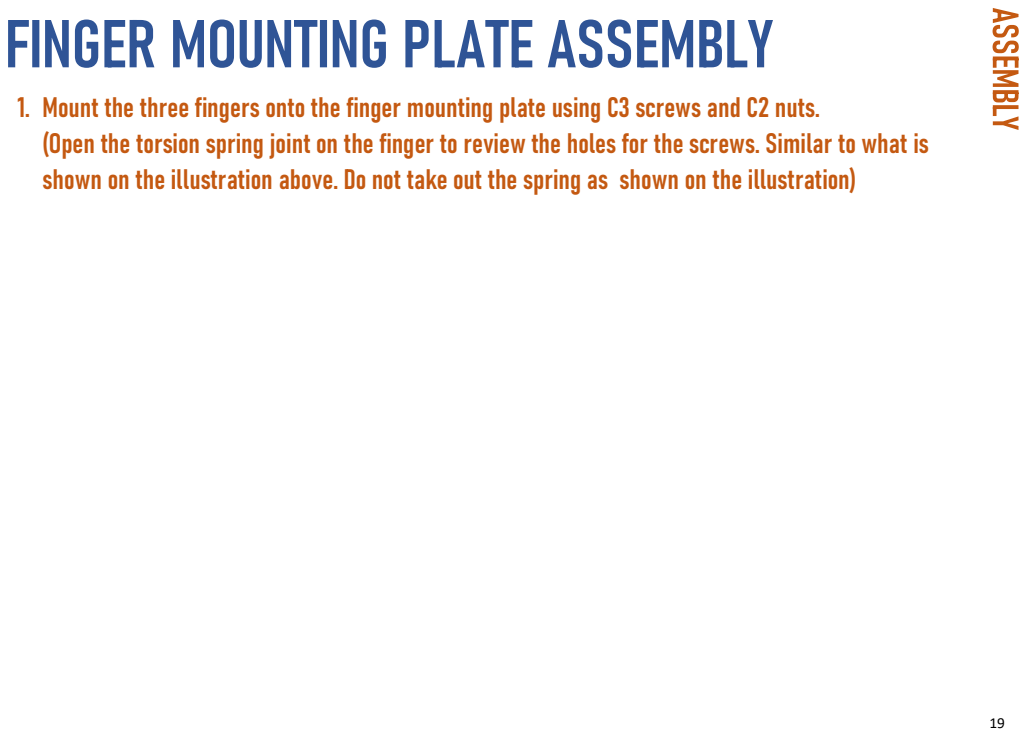
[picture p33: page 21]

1. Mount the three fingers onto the finger mounting plate using C3 screws and C2 nuts.
(Open the torsion spring joint on the finger to review the holes for the screws. Similar to what is
shown on the illustration above. Do not take out the spring as shown on the illustration)

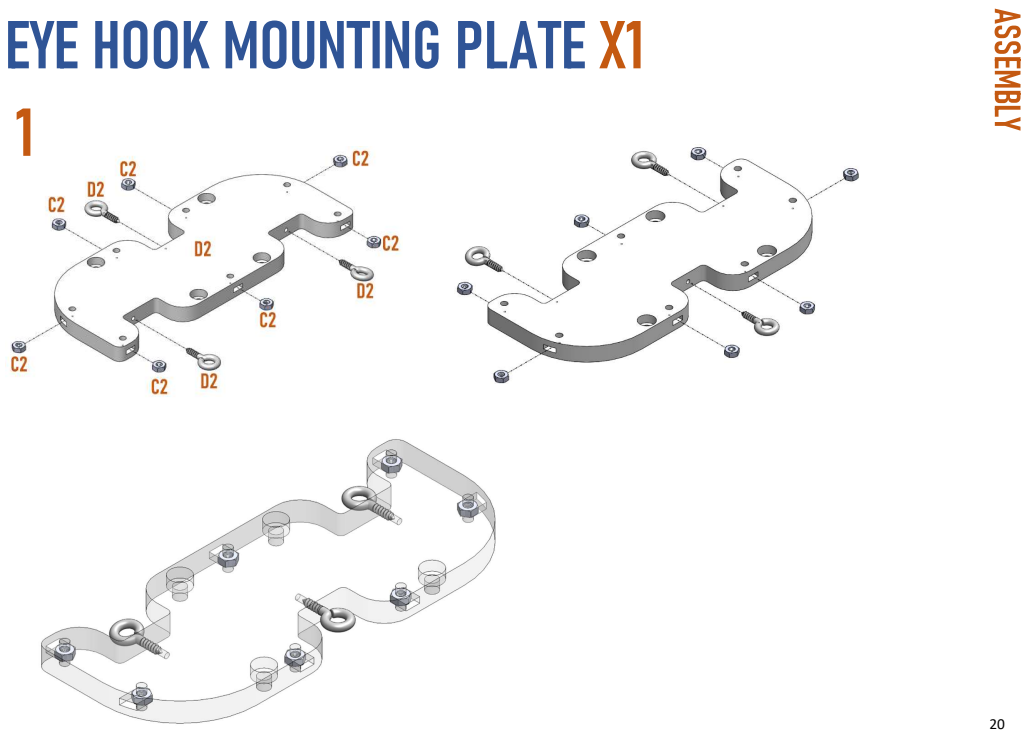
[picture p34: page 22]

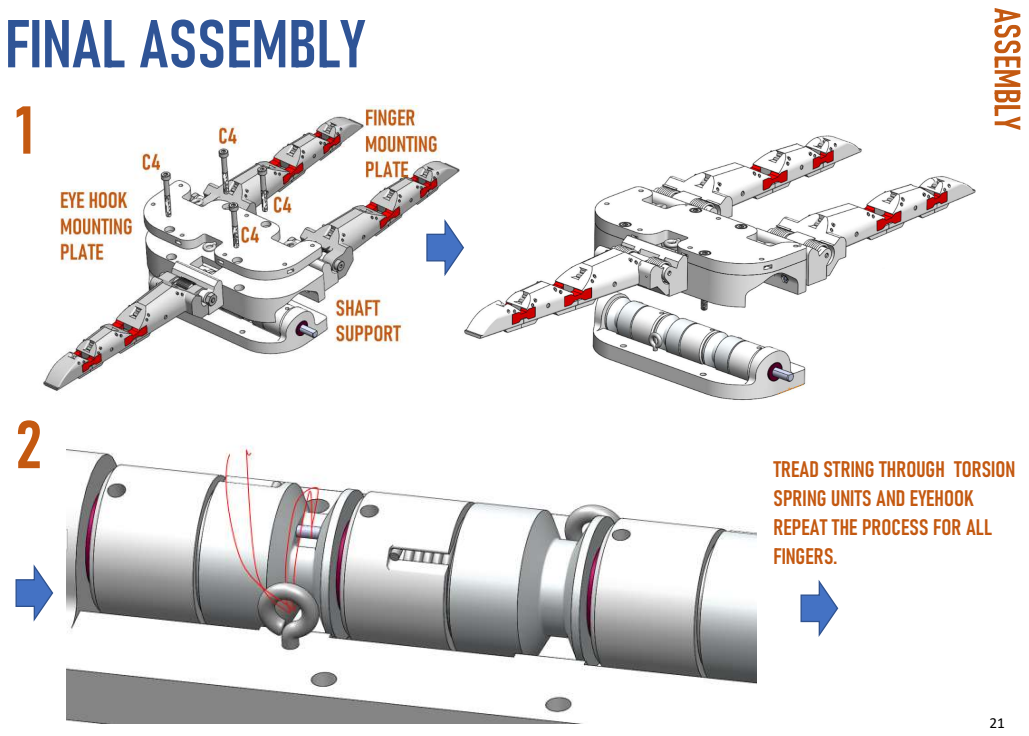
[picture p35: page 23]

TREAD STRING THROUGH TORSION
SPRING UNITS AND EYEHOOK
REPEAT THE PROCESS FOR ALL
FINGERS.

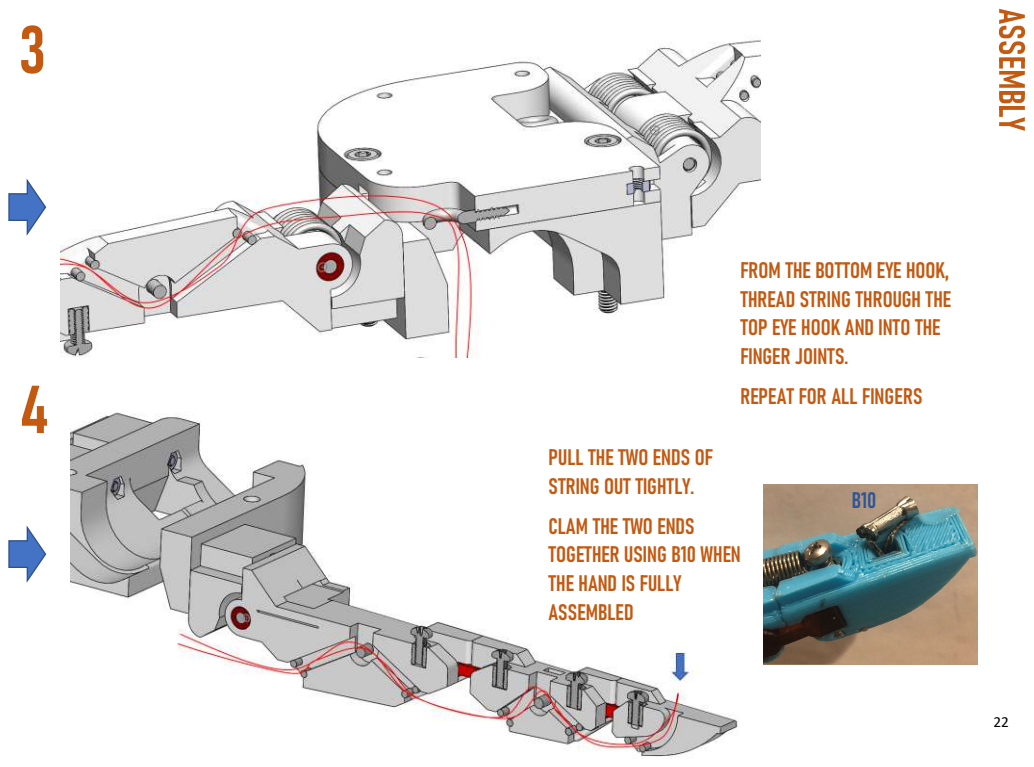
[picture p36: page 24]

FROM THE BOTTOM EYE HOOK,
THREAD STRING THROUGH THE
TOP EYE HOOK AND INTO THE
FINGER JOINTS.
REPEAT FOR ALL FINGERS

PULL THE TWO ENDS OF
STRING OUT TIGHTLY.
CLAM THE TWO ENDS
TOGETHER USING B10 WHEN
THE HAND IS FULLY
ASSEMBLED

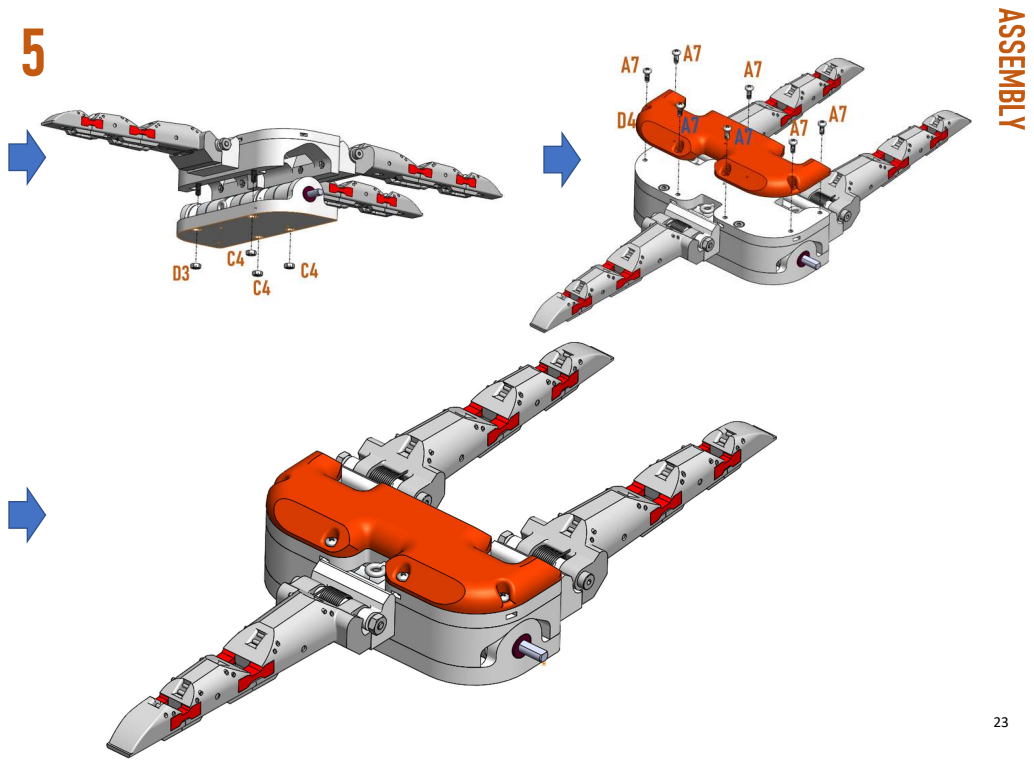
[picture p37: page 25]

24

1. Use C4 bolts to join the eyehook plate and finger mounting plate together.
2. Thread B13 Braided Dyneema Fishing line through the dowel pin on the torsion spring unit and eyehook next to it. ( The center point of the string should be on the dowel pin)
3. Thread the same string through the eyehook on the corresponding eyehook on the eyehook plate and then through the finger as shown in the illustration.
4. Repeat for the other fingers.
5. Pull the strings tight out of the slot at the end of the fingers and join the shaft support to the finger mounting plate by screwing the D3 nuts onto C4 bolts.
6. Clam the strings at the slots at the end of the fingers with crimps and cut of the rest of the strings.
7. Fix the palm plate onto the hand using A7 screws.

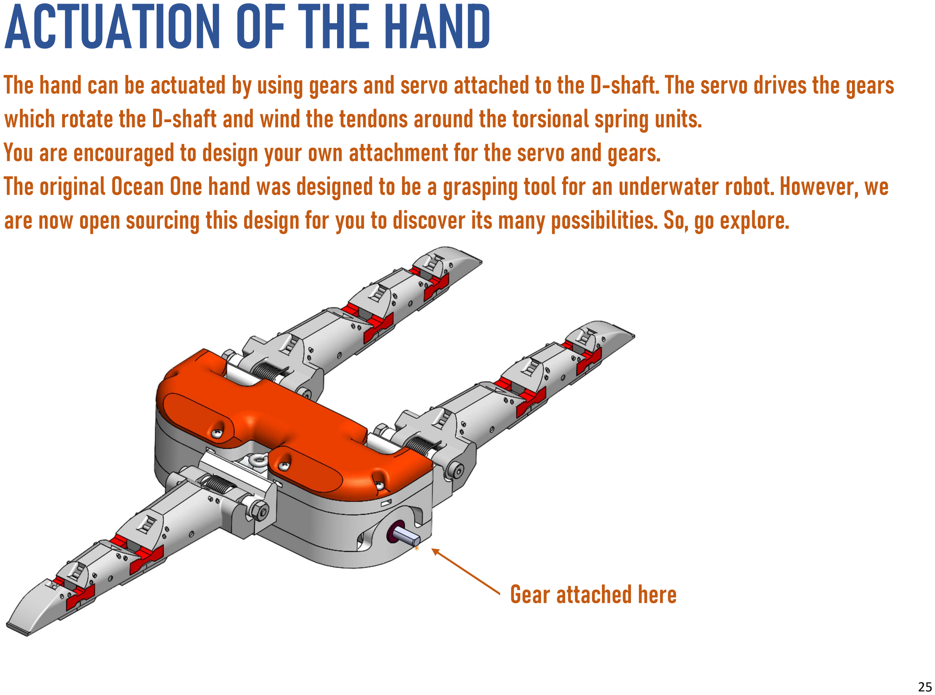
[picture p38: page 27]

25

The hand can be actuated by using gears and servo attached to the D-shaft. The servo drives the gears which rotate the D-shaft and wind the tendons around the torsional spring units.
You are encouraged to design your own attachment for the servo and gears.
The original Ocean One hand was designed to be a grasping tool for an underwater robot. However, we are now open sourcing this design for you to discover its many possibilities. So, go explore.

Gear attached here

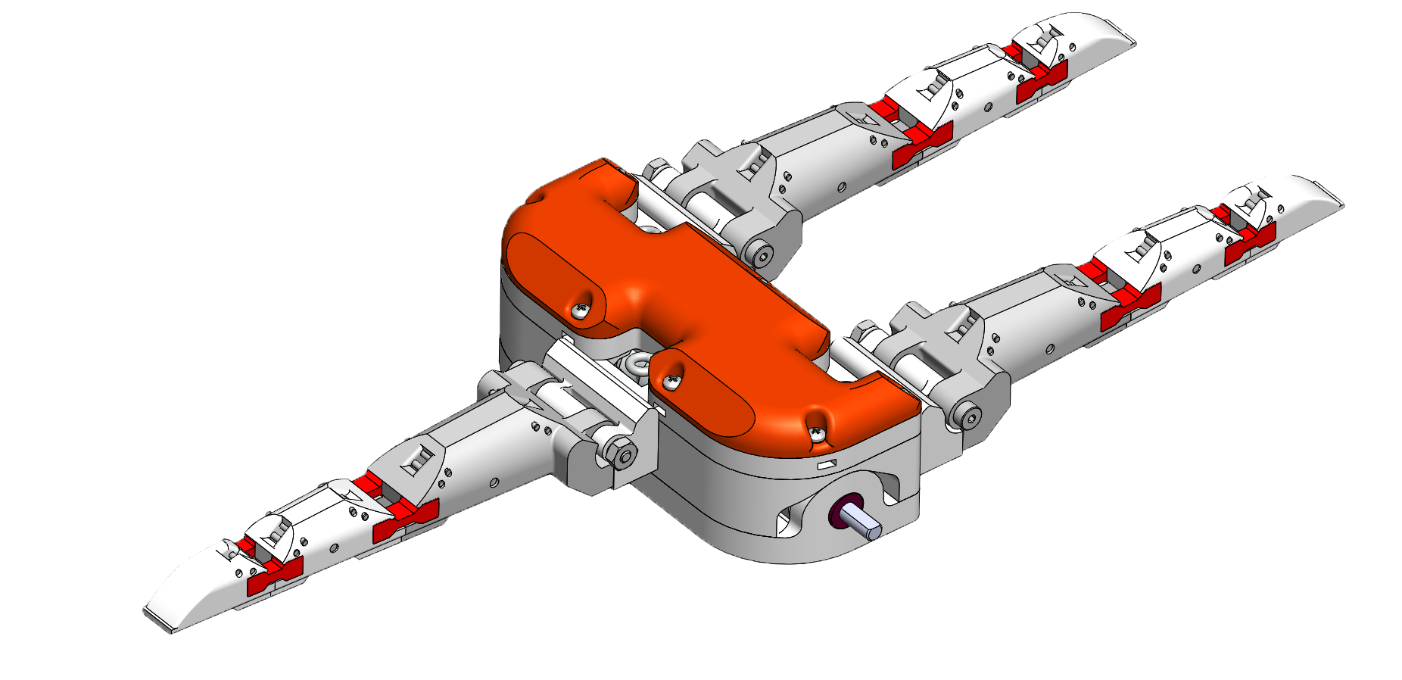
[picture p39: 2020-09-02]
Final Assembly/assembly pic.png

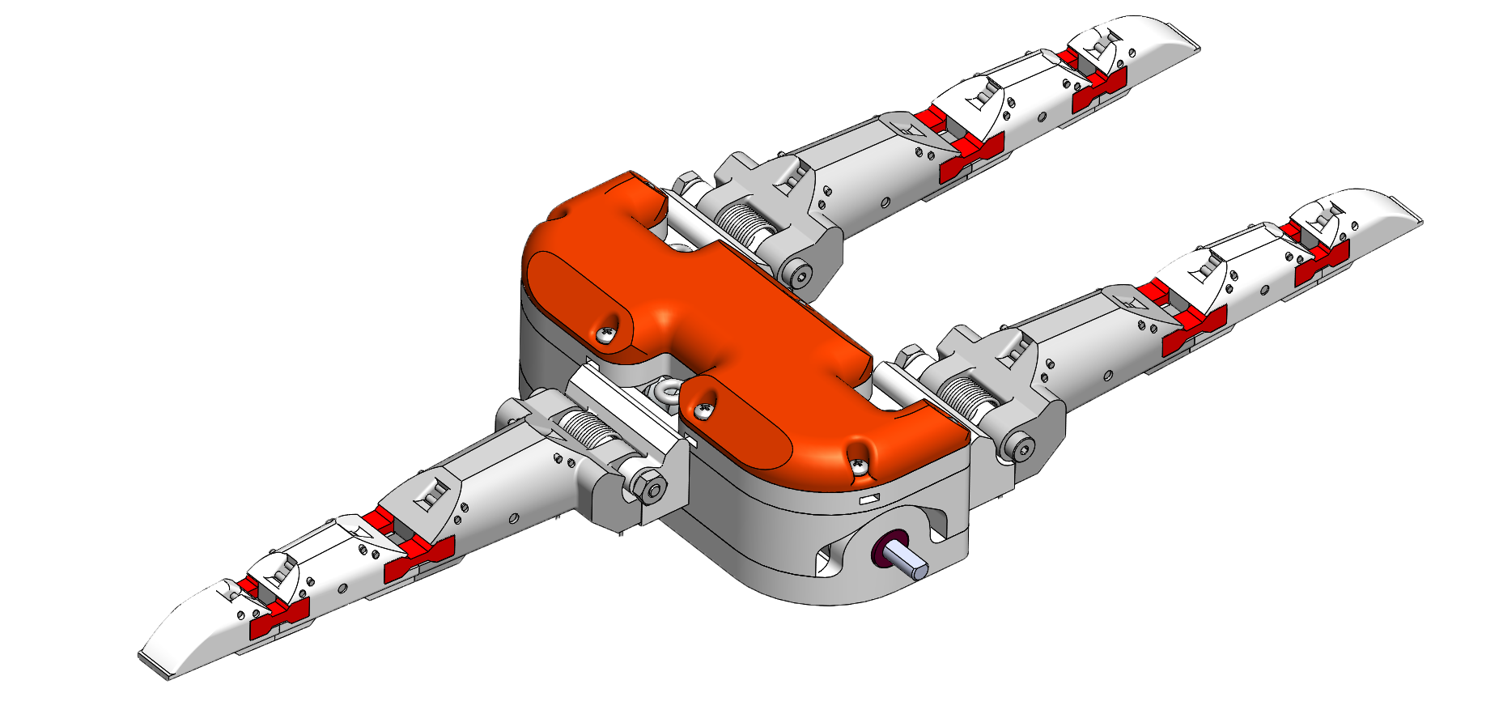
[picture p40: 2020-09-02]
Final Assembly/assembly pic 1.png

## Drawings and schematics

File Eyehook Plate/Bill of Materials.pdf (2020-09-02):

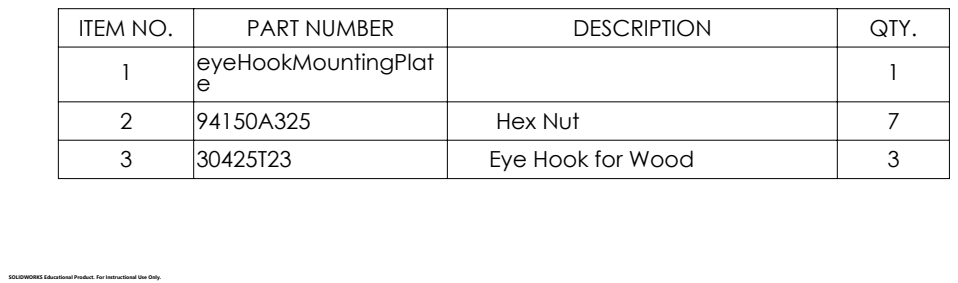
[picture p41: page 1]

ITEM NO. | PART NUMBER | DESCRIPTION | QTY.
1 | eyeHookMountingPlat e | | 1

2 | 94150A325 | Hex Nut | 7
3 | 30425T23 | Eye Hook for Wood | 3

SOLIDWORKS Educational Product. For Instructional Use Only.

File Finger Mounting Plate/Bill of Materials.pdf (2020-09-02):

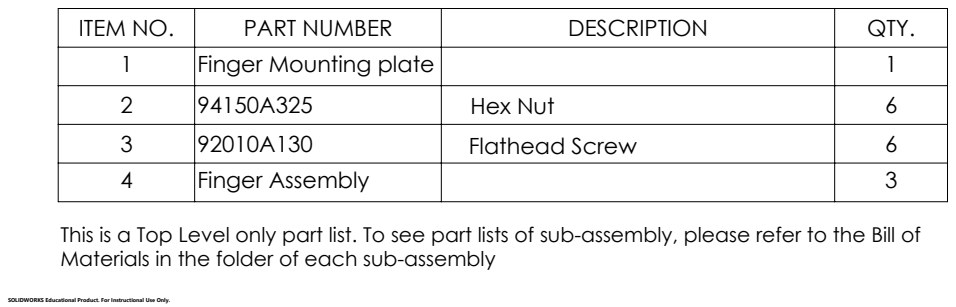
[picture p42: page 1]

ITEM NO. | PART NUMBER | DESCRIPTION | QTY.
1 | Finger Mounting plate | | 1
2 | 94150A325 | Hex Nut | 6
3 | 92010A130 | Flathead Screw | 6
4 | Finger Assembly | | 3

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

SOLIDWORKS Educational Product. For Instructional Use Only.
